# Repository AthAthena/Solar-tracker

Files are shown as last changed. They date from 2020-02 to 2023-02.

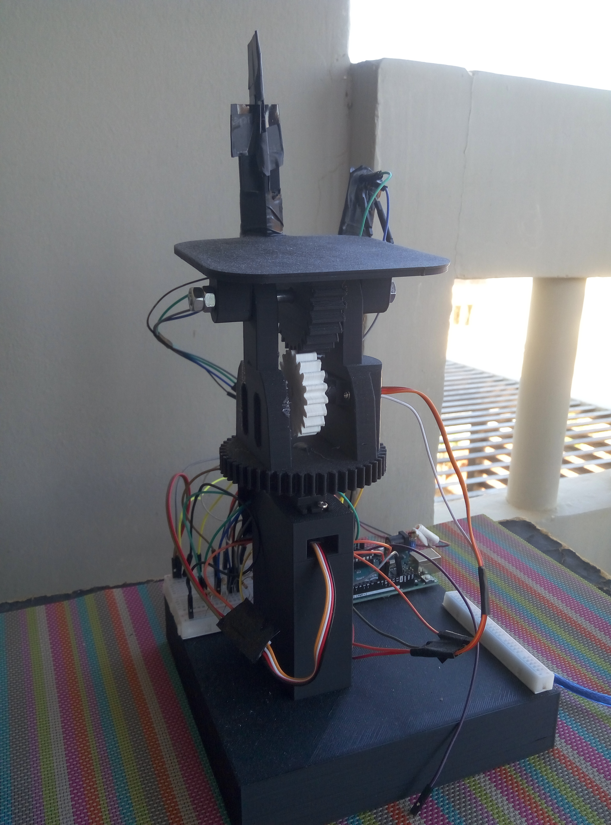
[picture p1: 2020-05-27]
P00513-165502[1].jpg

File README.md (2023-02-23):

ΕΠΑΛ ΚΙΣΑΜΟΥ-ΓΕΛ ΚΙΣΑΜΟΥ

ΛΙΓΑ ΛΟΓΙΑ ΓΙΑ ΤΗΝ ΠΕΡΙΠΕΤΕΙΑ ΤΗΣ ΚΑΤΑΣΚΕΥΗΣ ΜΑΣ
Η αναζήτηση άρχισε με σκοπό τη κατασκευή ενός solar tracker όπως του συναδέλφου https://www.thingiverse.com/thing:53321
ή https://www.instructables.com/id/Arduino-Solar-Tracker/ .
ΟΜΩΣ όλες αυτές οι κατασκευές είναι για εσωτερικό χώρο και για λόγους επίδειξης και όχι για ένα πραγματικό solar tracker.
Και εδώ μπήκαμε στην μεγάλη περιπέτεια κατασκευής ενός πραγματικού solar tracker και ως φυσική συνέπεια (ο καθηγητής μας είναι φυσικός και του αρέσει η αστροφυσική) και solar path finder- επιστημονικό εργαλείο εύρεσης των γωνίων που διαγράφει ο ΗΛΙΟΣ στην περιοχή μας.
ΚΑΙ ΑΝΑΣΧΕΔΙΑΣΑΜΕ ΤΑ ΠΑΝΤΑ ΕΞ ΑΡΧΗΣ!!!

Η ηλιακή ενέργεια αποτελεί ανανεώσιμη πηγή ενέργειας με πρόσφορη μέθοδο χρησιμοποίησή της τα φωτοβολταϊκά πάνελ. Όμως ο ήλιος αποδίδει τα μέγιστα μόνο όταν «πέφτει» κάθετα στο πάνελ, έτσι ψάχνουμε τρόπο να ακολουθεί το πάνελ τις ακτίνες του ήλιου. Ένας τρόπος παρακολούθησης του είναι με φωτοευαίσθητες αντιστάσεις οι οποίες παρακολουθούνται από τον μικροελεγκτή arduino και με servo ο μικροελεγκτής προσαρμόζει το πάνελ ώστε οι ακτίνες να πέφτουν κάθετα.

Υλικά (τελικός απολογισμός) :

1.arduino uno (https://grobotronics.com/funduino-uno-rev3-arduino-uno-compatible.html) = € 11.90 

2.   4 ldr (https://grobotronics.com/photo-resistor-ldr-5mm.html)=4*0,20=€ 0,80

3.  2 servo (link:  https://grobotronics.com/servo-small-5kg.cm-metal-gears-with-analog-feedback-feetech-fs9225m.html
https://grobotronics.com/analog-feedback-micro-servo-plastic-gear.html
 )=€9.90+€12.20=€21,10
 
4.wires (https://grobotronics.com/jumper-wires-15cm-female-to-male-pack-of-10.html ΚΑΙ https://grobotronics.com/jumper-wires-15cm-male-to-male-pack-of-10.html)=2*€1.80=€ 3,30

5..breadboard (link: https://grobotronics.com/breadboard-400-tie-point-white-half-size.html ) =€3.20

6.Bluetooth Module for Arduino - HC05 (https://grobotronics.com/bluetooth-module-for-arduino-hc05.html) =€6.80

7. 4 αντιστάσεις 1kohm (https://grobotronics.com/carbon-1-4w-5-1kohm.html) = €0,04

8.servo arm(https://grobotronics.com/servo-arm-double-5cm-horn-spline-25t.html)=€1.90

9.Πλαστικά γρανάζια απο 3D εκτυπωτή του εκφέ χανίων (ΤΑ STL ΑΡΧΕΙΑ ΠΕΡΙΛΑΜΒΑΝΟΝΤΑΙ ΩΣ ST1,ST2,..)
ΕΝΔΕΙΚΤΙΚΟ ΣΥΝΟΛΟ=€49,00

ΣΕ ΕΞΩΤΕΡΙΚΟ ΧΩΡΟ ΠΟΥ ΤΟ ΔΟΚΙΜΑΣΑΜΕ ΔΙΑΠΙΣΤΩΣΑΜΕ ΟΤΙ ΘΑ ΧΡΕΙΑΣΤΕΙ ΚΑΙ ΕΝΑ ΓΥΑΛΙΝΟ ΣΚΕΠΑΣΜΑ

ΠΕΡΙΓΡΑΦΗ ΠΡΟΒΛΗΜΑΤΟΣ
Η εποχή μας απαιτεί μεγάλα ενεργειακά αποθέματα , έτσι ένα αποδοτικό φωτοβολταικό πάνελ που ακολουθεί τον ήλιο μας δείχνει τον δρόμο στους κατασκευαστές φωτοβ.συστημάτων.Πόσο μάλλον όταν το πρότζεκτ μας καταγράφει τις γωνίες που δημιουργεί ο ήλιος στο στερέωμα στο καστέλι κισάμου και έτσι δείχνει ανα ημέρα και ώρα την κατάλληλη γωνία που πρέπει να έχει το φ. πάνελ για μέγιστη απόδοση.

Το μοίρασμα της γνώσης προτεραιότητα μας!
Μια επιστημονική εργασία αυτού του είδους εκπαιδεύει τους μελλοντικούς μας επιστήμονες στο διαθεματικό πλαίσιο STEM-ΘΕΤΙΚΕΣ ΕΠΙΣΤΗΜΕΣ-ΡΟΜΠΟΤΙΚΗ.
ΑΚΟΛΟΥΘΩΝΤΑΣ ΤΟ ΜΟΝΟΠΑΤΙ ΤΟΥ ΗΛΙΟΥ
Σε συνέχεια της προηγούμενης απάντησης η ιδέα μας είναι να κατασκευάσουμε ένα ηλιακό ανιχνευτή της πορείας του ήλιου που θα προσαρμόζει το φωτοβολταικό πάνελ μας κάθετα στις ακτίνες του ήλιου για να έχει την μέγιστη απόδοση και ταυτόχρονα θα καταγράφει τις γωνίες αυτές.Θα χρησιμοποιήσουμε 4 ldr φωτοαντιστάσεις-οι αισθητήρες φωτός που ανάλογα με το φως που λαμβάνουν θα δίνουν εντολή να στραφεί το πάνελ μας στη σωστή θέση- 2 σερβομηχανισμούς για να εκτελούν τις παραπάνω εντολές και θα αποτελούν συνάμα αισθητήρες κλίσης για την καταγραφή αυτών των γωνιών. Φυσικά και arduino που είναι ο εγκέφαλος της κατασκευής μας.
3D εκτυπωμένα εξαρτήματα θα δώσουν σταθερότητα και αποδοτικότητα στην κατασκευή μας.
Η ομάδα μας αποτελείται απο 3 μαθητές του ΓΕΛ Κισάμου β λυκείου με θαυμαστή όρεξη για μάθηση.
ΑΘΗΝΑ ΑΘΑΝΑΣΑΚΗ 
ΣΤΕΛΛΑ ΑΜΠΟΥΧΑΝΗ
ΣΠΥΡΟΣ ΕΙΡΗΝΑΚΗΣ
Τα κορίτσια είναι οι προγραμματίστριες του arduino και ο Σπύρος το πρακτικό μυαλό.
(Βέβαια οι απαιτήσεις του έργου ήταν να αναμιχθούν όλοι σε όλα τα στάδια της κατασκευής)
Ο Σπύρος βοήθησε και στο 3D σχεδιασμό εξαρτημάτων.
ΒΙΒΛΙΟΓΡΑΦΙΚΕΣ ΑΝΑΦΟΡΕΣ
1) https://en.wikipedia.org/wiki/Sun_path
2)https://en.wikipedia.org/wiki/Position_of_the_Sun
3)https://www.youtube.com/watch?v=lJVEubm9Ja8
4)https://www.instructables.com/id/Arduino-Solar-Tracker/

LINK ΠΟΥ ΒΟΗΘΗΣΕ ΣΤΗΝ ΒΑΘΜΟΝΟΜΗΣΗ-CALIBRATION SERVO : https://dronebotworkshop.com/analog-feedback-servo-motor/

ΓΙΑ ΤΟΝ ΔΙΑΓΩΝΙΣΜΟ ΤΗΣ ΕΛΛΑΚ ΠΑΡΑΠΕΜΠΩ ΣΤΟ GITHUB ΤΗΣ ΜΑΘΗΤΡΙΑΣ ΑΘΗΝΑΣ ΑΘΑΝΑΣΑΚΗ ΑΠΟ ΤΟΝ ΟΠΟΙΟ ΑΝΤΕΓΡΑΨΑ ΤΑ ΑΡΧΕΙΑ: https://github.com/Ampirath/Solar-Tracker
VIDEO LINK:  https://www.youtube.com/watch?v=TfUpVVRkGPY
ΜΑΘΗΤΕΣ : ΑΘΗΝΑ ΑΘΑΝΑΣΑΚΗ,ΣΤΕΛΛΑ ΑΜΠΟΥΧΑΝΗ ΚΑΙ ΣΠΥΡΟΣ ΕΙΡΗΝΑΚΗΣ-ΓΕΛ ΚΙΣΑΜΟΥ,ΕΠΑΛ ΚΙΣΑΜΟΥ

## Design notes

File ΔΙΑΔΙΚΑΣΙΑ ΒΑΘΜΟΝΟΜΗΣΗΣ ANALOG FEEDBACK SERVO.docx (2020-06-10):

ΔΙΑΔΙΚΑΣΙΑ ΒΑΘΜΟΝΟΜΗΣΗΣ ANALOG FEEDBACK SERVO

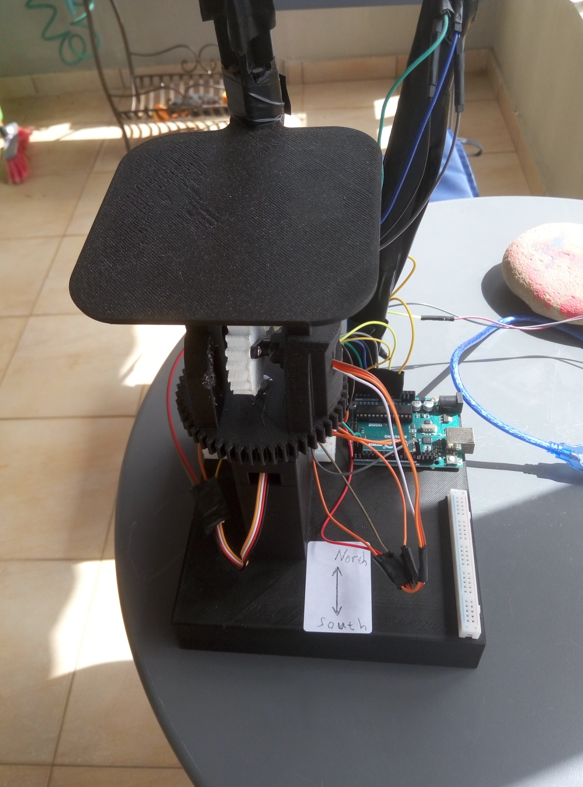
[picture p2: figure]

Κατά την τοποθέτηση προσέχουμε το κάτω servo να χει περιθώριο κινήσεων σε σχέση με τον νότο-south(βλέπε εικόνα) δεξιά –ανατολή 90⁰ ,αριστερά- δύση 90⁰ και με το πρόγραμμα recalibrationhorizontalservo.ino έχοντας σημαδέψει τις 90⁰ δεξιά αριστερά , βάζοντας σε //comment τις 35 και 36 γραμμές βρίσκουμε την αληθή αντιστοίχηση μεταξύ feedbackValue και γωνίας. Έπειτα προσθέτουμε τις γραμμές *

## feedbackValue = analogRead(feedbackPin);

## angle=map(feedbackValueh,84,424,-90,90);

## Βάζοντας στην θέση 84,424 τις τιμές που θα βρείτε εσείς και αντιστοιχούν στις γωνίες -90 ,90.

## *Τις γραμμές αυτές του κώδικα τις τοποθετείτε στην ίδια θέση του mainprogram.

## Αντίστοιχα εργαζόμαστε για το πάνω –vertical servo .Το πρόγραμμα CALIBRATIONANALOGSERVOvertical.ino ουσιαστικά είναι ίδιο με το recalibrationhorizontalservo.ino.

## Στο παρακάτω link αντλήσαμε πληροφορίες για την βαθμονόμηση αλλά και για αυτά τα analogfeedback servo:

## https://dronebotworkshop.com/analog-feedback-servo-motor/

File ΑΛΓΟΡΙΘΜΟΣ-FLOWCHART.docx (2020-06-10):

ΕΑΝ ΠΑΝΩ>ΚΑΤΩ

VERT.SERVO ΠΑΝΩ-ΒΟΡΕΙΑ

ΑΛΛΙΩΣ ΕΑΝ ΚΑΤΩ >ΠΑΝΩ

VERT.SERVO ΚΑΤΩ-ΝΟΤΙΑ

VERT,SERVO ΚΑΤΩ

ΕΑΝ ΟΙ ΔΕΞΙΟΙ-ΑΡΙΣΤΕΡΟΙ ΑΙΣΘΗΤΗΡΕΣ ΕΧΟΥΝ ΜΕΓΑΛΥΤΕΡΗ ΔΙΑΦΟΡΑ ΑΠΟ ΤΗΝ ΕΠΙΤΡΕΠΟΜΕΝΗ

↓

ΚΑΤΕΓΡΑΨΕ ΓΩΝΙΕΣ

1) γωνία ύψους-altitude και

2) azimuth-ΑΖΙΜΟΥΘΙΟ

VOID SETUP (ΤΡΕΧΕΙ ΜΙΑ ΦΟΡΑ)

ΑΡΧΙΚΟΠΟΙΗΣΗ ΣΕΙΡΙΑΚΗΣ ΕΠΙΚΟΙΝΩΝΙΑΣ

horizontal SERVO.attach PIN

vertical SERVO.attach PIN

ΧΡΗΣΙΜΟΠΟΙΗΣΗ SERVO ΒΙΒΛΙΟΘΗΚΗΣ

ΚΑΘΟΡΙΣΜΟΣ PIN ΓΙΑ ΚΑΤΩ-HORIZONTAL SERVO ΚΑΙ FEEDBACK ANALOG PIN ΚΑΙ ΟΡΙΑ-LIMITS SERVO

ΚΑΘΟΡΙΣΜΟΣ PIN ΓΙΑ ΠΑΝΩ-VERTICAL SERVO ΚΑΙ FEEDBACK ANALOG PIN ΚΑΙ ΟΡΙΑ-LIMOTS SERVO

ΚΑΘΟΡΙΣΜΟΣ ANALOG PIN ΓΙΑ LDR SENSOR

ΔΙΑΒΑΣΜΑ ΑΠΟ LDR SENSORS ΚΑΙ ΥΠΟΛΟΓΙΣΜΟΣ ΜΕΣΩΝ ΤΙΜΩΝ LDR ,ΠΑΝΩ-ΚΑΤΩ ΚΑΙ ΔΕΞΙΑ ΑΡΙΣΤΕΡΑ

ΕΑΝ ΟΙ ΠΑΝΩ- ΚΑΤΩ ΑΙΣΘΗΤΗΡΕΣ ΕΧΟΥΝ ΜΕΓΑΛΥΤΕΡΗ ΔΙΑΦΟΡΑ ΑΠΟ ΤΗΝ ΕΠΙΤΡΕΠΟΜΕΝΗ

↓

ΚΑΤΕΓΡΑΨΕ ΓΩΝΙΕΣ

1) γωνία ύψους-altitude και

2) azimuth-ΑΖΙΜΟΥΘΙΟ

ΕΑΝ ΔΕΞΙΟΙ>ΑΡΙΣΤΕΡΟΙ

HORIZ.SERVO ΔΕΞΙΑ-ΑΝΑΤΟΛΙΚΑ

ΑΛΛΙΩΣ ΕΑΝ ΑΡΙΣΤΕΡΟΙ>ΔΕΞΙΟΙ

HORIZ.SERVO ΑΡΙΣΤΕΡΑ-ΔΥΤΙΚΑ

VOID LOOP (ΕΠΑΝΑΛΑΜΒΑΝΟΜΕΜΗ ΛΟΥΠΑ)

MAP-ΧΑΡΤΗΣ ΠΟΥ ΠΡΟΕΚΥΨΕ ΜΕΤΑ ΑΠΟ CALIBRATION Α)ΓΙΑ ΑΖΙΜΟΥΘΙΟ-AZIMUTH

,, Β)ΓΙΑ ΥΨΟΣ-ALTITUDE

ΑΡΧΗ ΠΡΟΓΡΑΜΜΑΤΟΣ

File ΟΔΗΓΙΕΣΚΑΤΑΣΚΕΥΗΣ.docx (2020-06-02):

Υλικά (τελικός απολογισμός) :

1.arduino uno (https://grobotronics.com/funduino-uno-rev3-arduino-uno-compatible.html) = € 11.90
2. 4 ldr (https://grobotronics.com/photo-resistor-ldr-5mm.html)=4*0,20=€ 0,80
3. 2 servo (link: https://grobotronics.com/servo-small-5kg.cm-metal-gears-with-analog-feedback-feetech-fs9225m.html
https://grobotronics.com/analog-feedback-micro-servo-plastic-gear.html
)=€9.90+€12.20=€21,10
4.wires (https://grobotronics.com/jumper-wires-15cm-female-to-male-pack-of-10.html ΚΑΙ https://grobotronics.com/jumper-wires-15cm-male-to-male-pack-of-10.html)=2*€1.80=€ 3,30
5..breadboard (link: https://grobotronics.com/breadboard-400-tie-point-white-half-size.html ) =€3.20
6.Bluetooth Module for Arduino – HC05 (https://grobotronics.com/bluetooth-module-for-arduino-hc05.html) =€6.80

7. 4 αντιστάσεις 1kohm (https://grobotronics.com/carbon-1-4w-5-1kohm.html) = €0,04

8.servo arm(https://grobotronics.com/servo-arm-double-5cm-horn-spline-25t.html)=€1.90
9.Πλαστικά γρανάζια απο 3D εκτυπωτή του εκφέ χανίων (ΤΑ STL ΑΡΧΕΙΑ ΠΕΡΙΛΑΜΒΑΝΟΝΤΑΙ ΩΣ ST1,ST2,..)
ΕΝΔΕΙΚΤΙΚΟ ΣΥΝΟΛΟ=€49,00

Η ιδέα μας είναι να κατασκευάσουμε ένα ηλιακό ανιχνευτή της πορείας του ήλιου που θα προσαρμόζει το φωτοβολταικό πάνελ μας κάθετα στις ακτίνες του ήλιου για να έχει την μέγιστη απόδοση και ταυτόχρονα θα καταγράφει τις γωνίες αυτές. Θα χρησιμοποιήσουμε 4 ldr φωτοαντιστάσεις-οι αισθητήρες φωτός που ανάλογα με το φως που λαμβάνουν θα δίνουν εντολή να στραφεί το πάνελ μας στη σωστή θέση- 2 σερβομηχανισμούς για να εκτελούν τις παραπάνω εντολές και θα αποτελούν συνάμα αισθητήρες κλίσης για την καταγραφή αυτών των γωνιών. Φυσικά και arduino που είναι ο εγκέφαλος της κατασκευής μας. 3D εκτυπωμένα εξαρτήματα θα δώσουν σταθερότητα και αποδοτικότητα στην κατασκευή μας.

ΚΑΤΑΣΚΕΥΗ

Τα σχεδιασμένα 3d εξαρτήματα απο την ομάδα μας θα τα βρείτε ως stl αρχεία στο github.Τα servo που είναι στη λίστα μας «κουμπώνουν» ακριβώς στα παραπάνω εξαρτήματα.

Το servo : https://grobotronics.com/servo-small-5kg.cm-metal-gears-with-analog-feedback-feetech-fs9225m.html

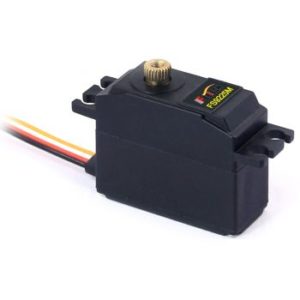
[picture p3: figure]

«κουμπώνει» στο 3d εξάρτημα base.stl (ή stl 1).

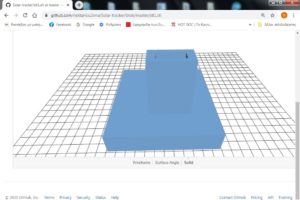
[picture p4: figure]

Πάνω στο servo βάζουμε το servo arm (https://grobotronics.com/servo-arm-double-5cm-horn-spline-25t.html) .

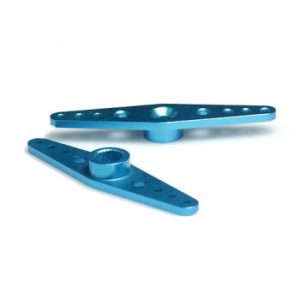
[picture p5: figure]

ΟΠΩΣ ΣΤΗΝ ΕΙΚΟΝΑ 1

ΕΙΚΟΝΑ1:

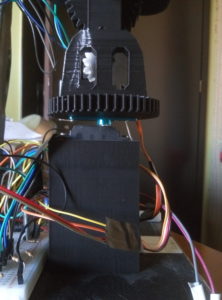
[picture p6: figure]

Πάνω στο servoarm βιδώνουμε το 3d εξάρτημα panel-mount.stl (ή stl2)

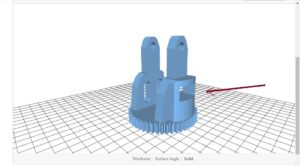
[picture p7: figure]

και τοποθετούμε το 2ο servo (εκεί που δείχνει το βέλος)

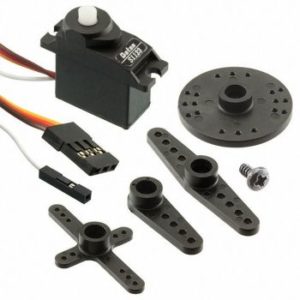
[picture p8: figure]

στο κατάλληλο άνοιγμα του panel-mount.stl, όπως την εικόνα 2:

ΕΙΚΟΝΑ2

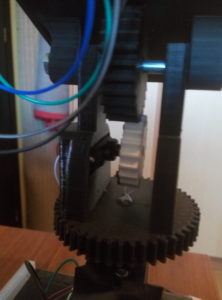
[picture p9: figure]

Στο 2ο servo βιδώνουμε το Vertical_Servo_Gear.stl (ή stl5, το άσπρο στην εικόνα2 )

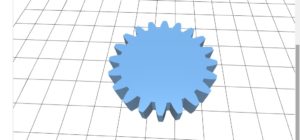
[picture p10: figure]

όπως στην εικόνα 2.

Στο Panel_Bracket2.stl(ή stl4)

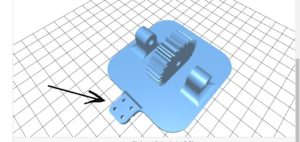
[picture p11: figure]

τοποθετούμε το LDR DIVIDER HIGH.stl(ή stl3) εκεί που δείχνει το βέλος (έχει υποδοχή να το δεχτεί και ας μην φαίνεται στην πανω εικόνα).

LDR DIVIDER HIGH.stl:

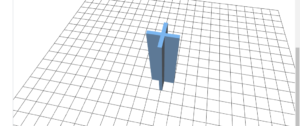
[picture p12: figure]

Τέλος με την κατάλληλη βίδα 4mm με μήκος 9cm και τα αντίστοιχα παξιμάδια τοποθετούμε το Panel_Bracket2.stl όπως στην εικόνα 2.

Η συνδεσμολογία πρέπει να γίνει όπως

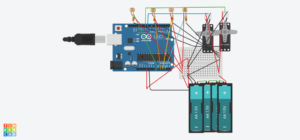
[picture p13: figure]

ΟΛΑ TA ΑΡΧΕΙΑ ΒΡΙΣΚΟΝΤΑΙ ΣΤΟ GITHUB ΜΕ ΜΕΓΑΛΥΤΕΡΗ ΑΝΑΛΥΣΗ.

Έπειτα έπρεπε να βαθμονομήσουμε τα servo ώστε να μετράνε την σωστή γωνία και σε αυτήν την επίπονη διαδικασία βοήθησε το 2ο link.

Ο διαιρέτης τάσης που φαίνεται στο κύκλωμα που βρίσκεται στο github λειτούργησε καλά τελικά σε εξωτερικό χώρο με αντιστάσεις 1 kohm(4 αντιστάσεις).

ΒΙΒΛΙΟΓΡΑΦΙΚΕΣ ΑΝΑΦΟΡΕΣ

1. https://en.wikipedia.org/wiki/Sun_path 2)https://en.wikipedia.org/wiki/Position_of_the_Sun 3)https://www.youtube.com/watch?v=lJVEubm9Ja8 4)https://www.instructables.com/id/Arduino-Solar-Tracker/
2. LINK ΠΟΥ ΒΟΗΘΗΣΕ ΣΤΗΝ ΒΑΘΜΟΝΟΜΗΣΗ-CALIBRATION SERVO : https://dronebotworkshop.com/analog-feedback-servo-motor/

ΣΤΟ LINK ΠΟΥ ΑΚΟΛΟΥΘΕΙ ΚΑΙ ΑΝΗΚΕΙ ΟΠΩΣ ΚΑΙ ΔΗΜΙΟΥΡΓΗΘΗΚΕ ΑΠΟ ΤΗΝ ΟΜΑΔΑ ΤΩΝ ΜΑΘΗΤΩΝ ΠΟΥ ΕΡΓΑΣΤΗΚΕ ΓΙ ΑΥΤΟ ΤΟ PROJECT ΕΙΝΑΙ ΤΟΠΟΘΕΤΗΜΕΝΑ ΟΛΑ ΤΑ ΑΡΧΕΙΑ ΠΟΥ ΕΙΝΑΙ ΑΝΑΓΚΑΙΑ ΓΙΑ ΤΗΝ ΚΑΤΑΝΟΗΣΗ ΚΑΙ ΚΑΤΑΣΚΕΥΗ ΑΝΑΛΟΓΟΥ ΕΓΧΕΙΡΗΜΑΤΟΣ LINK: https://github.com/Ampirath/Solar-Tracker

LINK VIDEO ΠΟΥ ΦΤΙΑΧΤΗΚΕ ΑΠΟ ΤΑ ΠΑΙΔΙΑ: https://www.youtube.com/watch?v=TfUpVVRkGPY

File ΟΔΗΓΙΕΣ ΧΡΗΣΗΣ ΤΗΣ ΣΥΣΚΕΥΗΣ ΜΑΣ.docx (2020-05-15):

ΟΔΗΓΙΕΣ ΧΡΗΣΗΣ ΤΗΣ ΣΥΣΚΕΥΗΣ ΜΑΣ-Η ΕΚΔΟΧΗ ΜΕ ΤΑ ANALOG FEEDBACK SERVO

Εφόσον έχουμε εκτυπώσει τα 3D εξαρτήματά μας και έχουμε πραγματοποιήσει την συνδεσμολογία που φαίνεται στο png αρχείο (και στο brd από το tinkercad) φορτώνουμε στο arduino το προγραμμά μας (MAINPROGRAM.ino).

Επειτα έχοντας κατεβάσει στο κινητό μας από το google play ή από όπου θέλουμε μια εφαρμογή που μας δείχνει τον πραγματικό βορά ( gps true north) τοποθετούμε την συσκευή όπως την εικόνα που είναι στην επόμενη σελίδα (παρατηρήστε το άσπρο αυτοκόλλητο που δείχνει την σωστή τοποθέτηση).


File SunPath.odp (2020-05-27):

## Βρίσκοντας το μονοπάτι του ήλιου

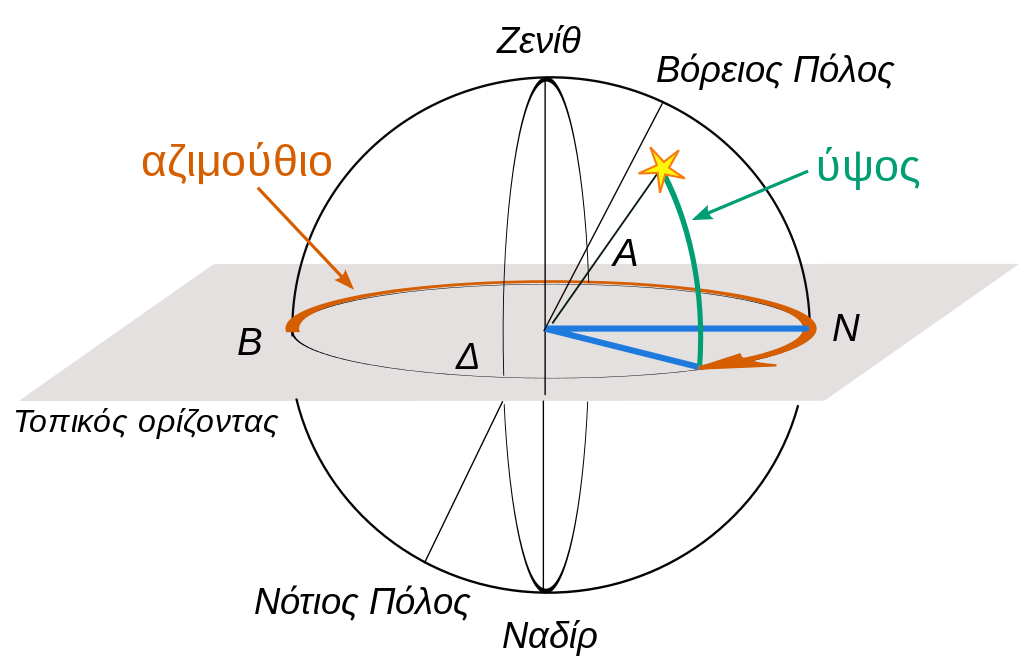
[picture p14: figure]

## Η διαδρομή του ήλιου

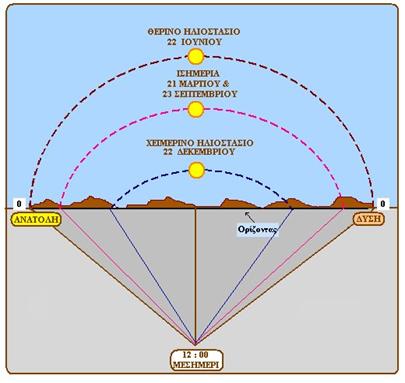
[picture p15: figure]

## Ύψος ήλιου (κλίση επιφάνειας) (altitude)

  Το ύψος του ήλιου αναφέρεται στη γωνία που σχηματίζει ο ήλιος με τον ορίζοντα της Γης. Αφού ειναι γωνία, μετριέται σε μήρες.
  Η κλίση είναι 0° στην ανατολή του ηλίου και στην δύση του και μπορεί να φτάσει τις 90° (ζενίθ) το μεσημέρι, σε μέρη κοντά στον ισημερινό.
  Λόγω της κλίσης του άξονα περιστροφής της γης η θέση του ήλιου στον ουρανό του ισημερινού το μεσημέρι θα αποκλίνει στη διάρκεια του έτους κατά +/- 23.5 μοίρες από το απολύτως κάθετο (ζενίθ).

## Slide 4

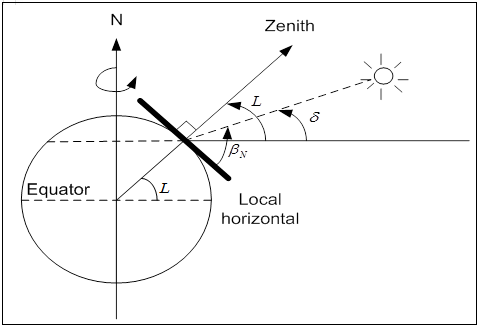
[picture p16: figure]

## Γωνία αζιμούθιου (azimuth)

  Είναι η γωνία προς την οποία ειναι στραμμένη μια επιφάνεια.
  Συνήθως μετριέται απο το Βορρά (0° / 360°) προς την Ανατολή.

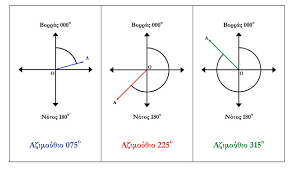
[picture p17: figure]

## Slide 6

  Ή μπορούμε ανάλογα το ημισφαίριο να το ορίσουμε διαφορετικά.
  Για τοποθεσίες του βόρειου ηµισφαιρίου µηδενική τιµή του αζιμούθιου γ αντιστοιχεί σε νότια κατεύθυνση, θετικές τιµές του αναφέρονται σε δυτικούς προσανατολισµούς, και αρνητικές τιµές του γ σε ανατολικούς προσανατολισµούς.

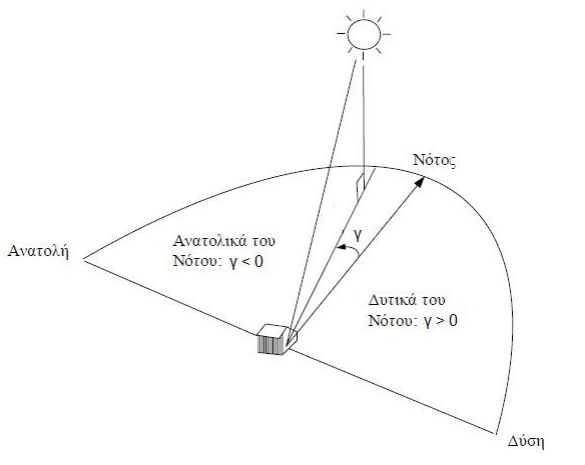
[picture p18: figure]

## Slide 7

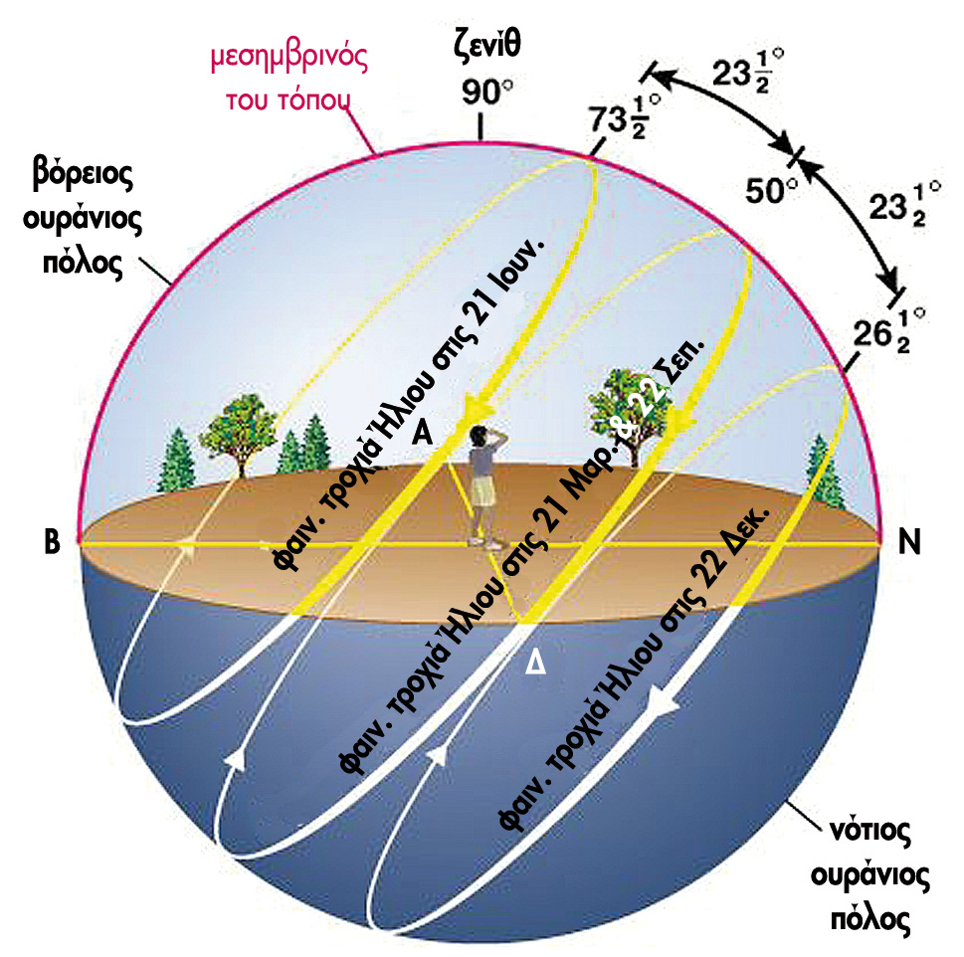
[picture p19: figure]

  Αθηνά Μαρία Αθανασάκη – ΓΕΛ Κισάμου

## ΠΗΓΕΣ

- Motions of the Sun simulator (https://ccnmtl.github.io/astro-simulations/sun-motion-simulator/)
- Sun Path (wikipedia) (https://en.wikipedia.org/wiki/Sun_path)
- Position of the Sun (wikipedia) (https://en.wikipedia.org/wiki/Position_of_the_Sun)
- Solar altitude (https://sciencing.com/solar-altitude-23364.html)
- Solar Zenith Angle (wikipedia) (https://en.wikipedia.org/wiki/Solar_zenith_angle)
- Solar Azimuth (wikipedia) (https://en.wikipedia.org/wiki/Solar_azimuth_angle)
- Διάγραμμα μονοπατιού (https://www.sunearthtools.com/dp/tools/pos_sun.php)
- Μονοπάτι του Ήλιου στην Αθήνα (https://acomelectronics.com/forum/viewtopic.php?t=20)
- Ηλιακή Ακτινοβολία - Γεωμετρία

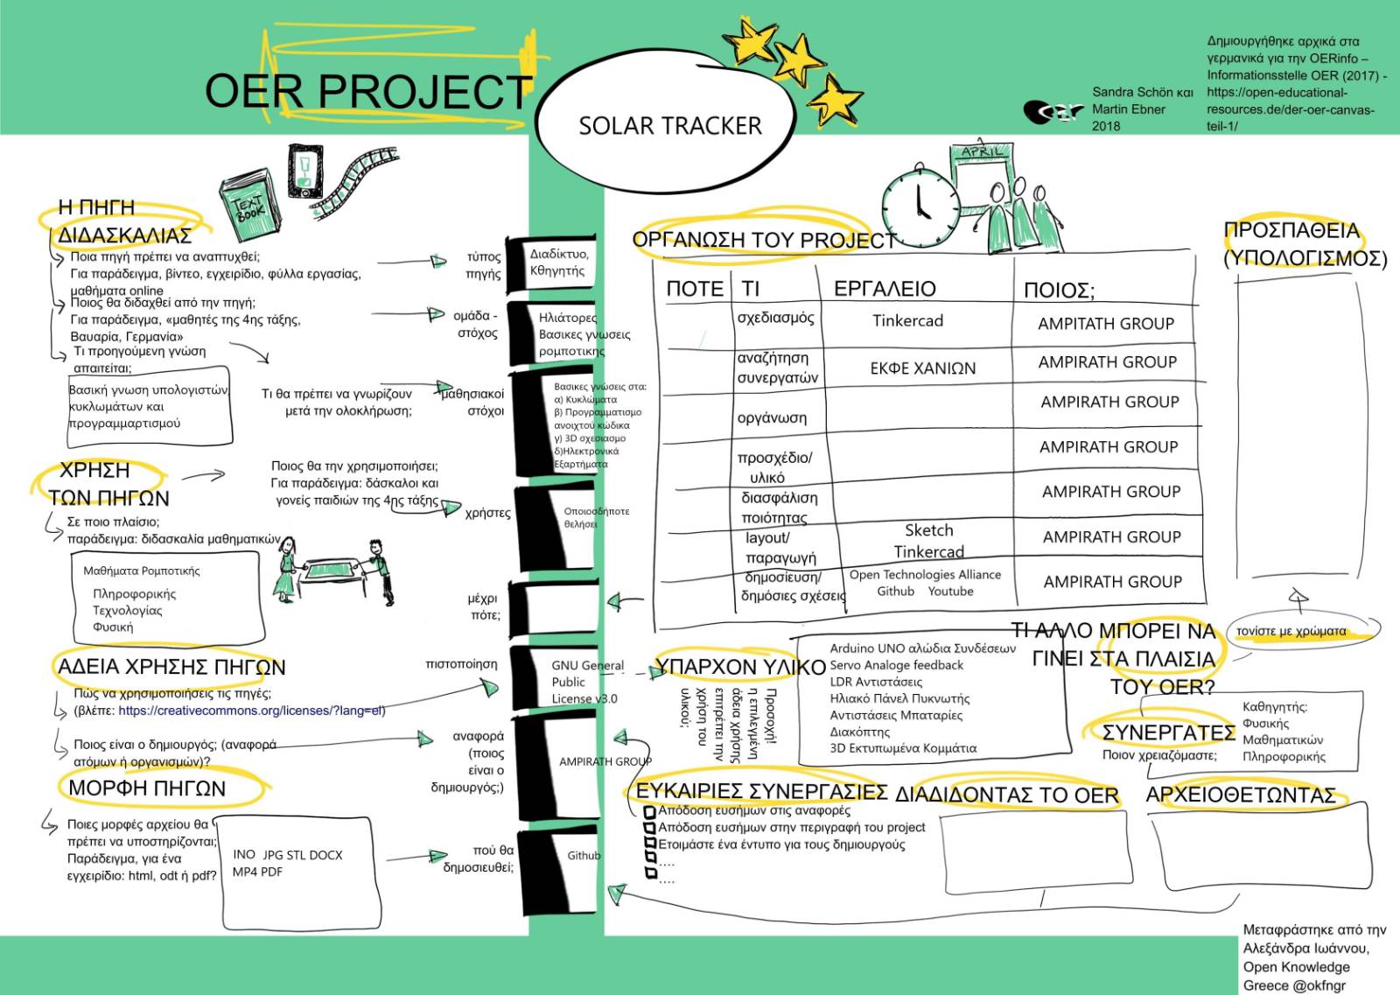
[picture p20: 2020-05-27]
OERCANVAS.jpg

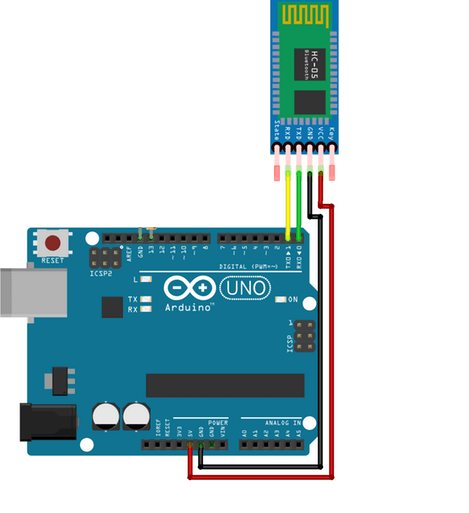
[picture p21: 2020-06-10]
hc-05-connection-Circuit.png

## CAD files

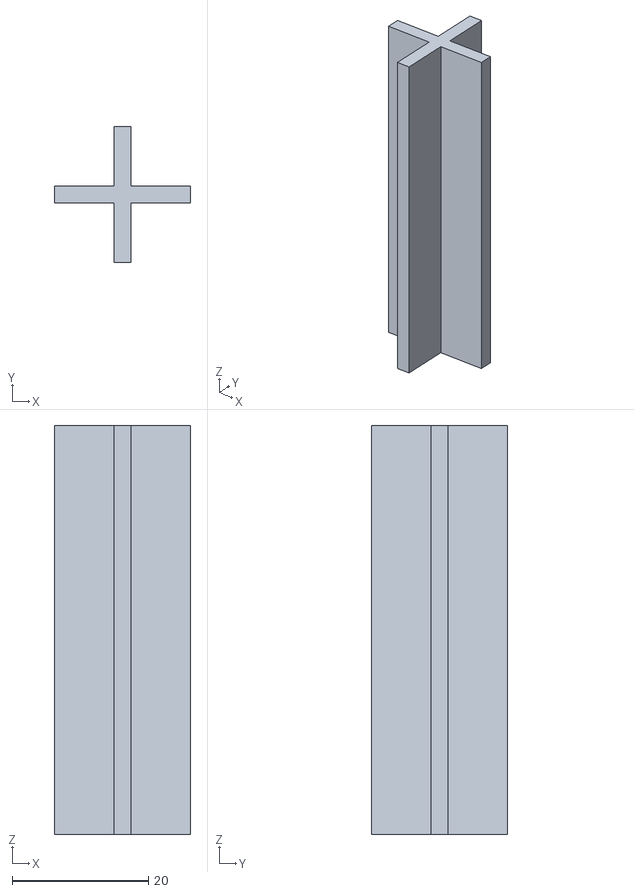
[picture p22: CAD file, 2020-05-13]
stl3.stl
20.0 x 20.0 x 60.0

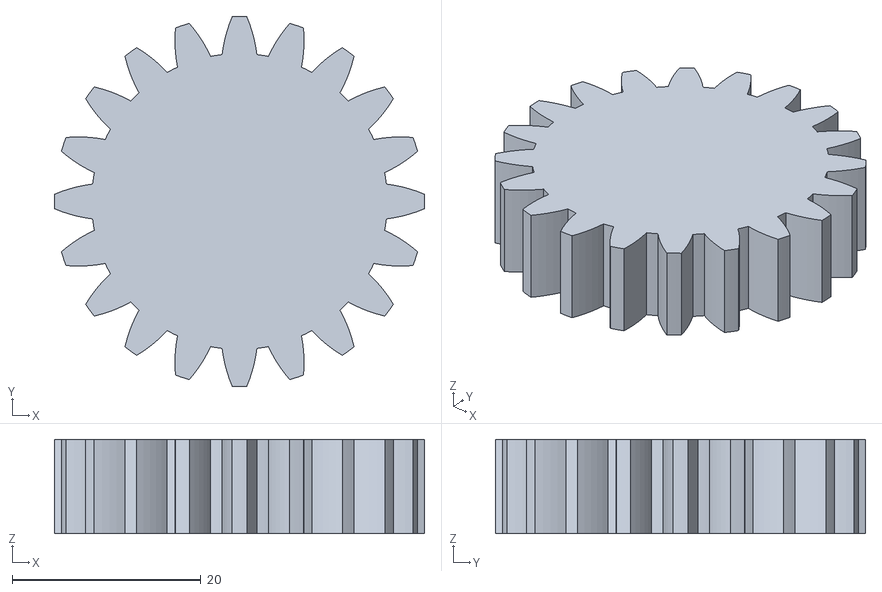
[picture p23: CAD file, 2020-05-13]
stl5.stl
39.2 x 39.2 x 10.0

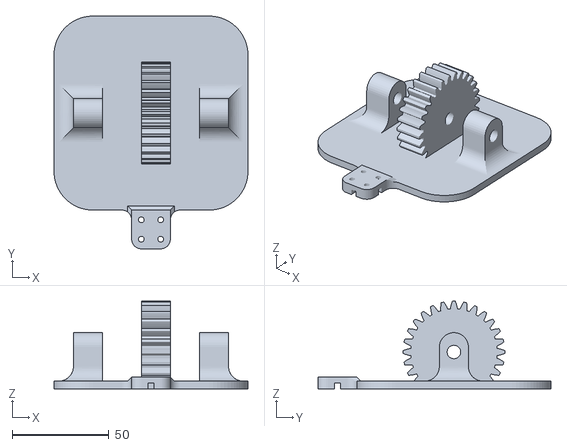
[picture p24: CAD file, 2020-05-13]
stl4.stl
100.0 x 120.0 x 45.2

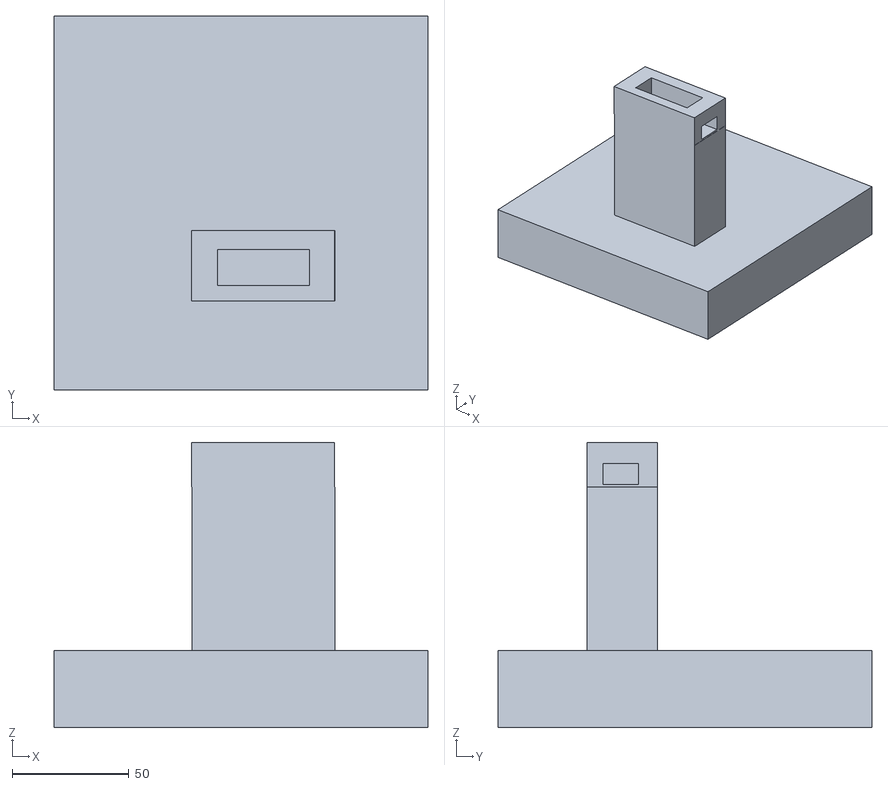
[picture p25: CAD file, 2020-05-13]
stl1.stl
160.0 x 160.0 x 122.1

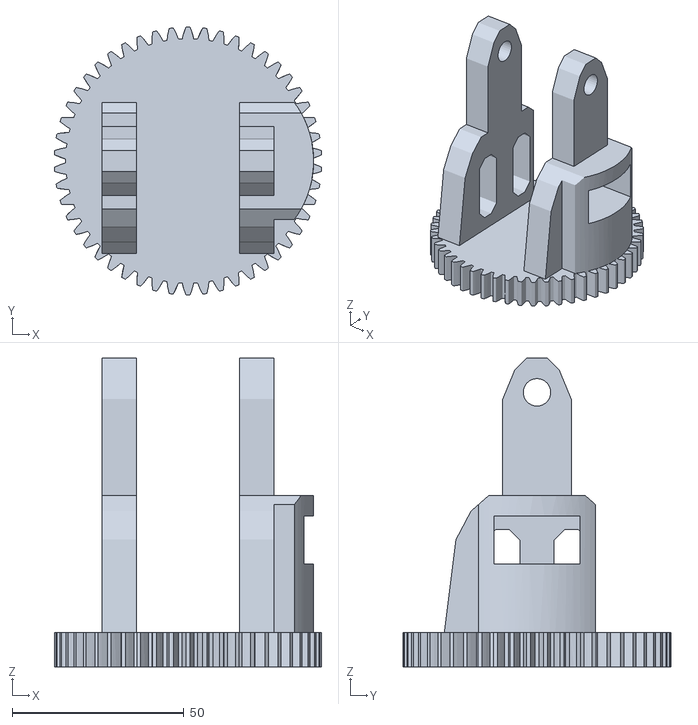
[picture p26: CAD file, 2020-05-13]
stl2.stl
77.9 x 78.0 x 90.0

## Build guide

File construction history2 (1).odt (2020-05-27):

Solar Path Finder

Ιστορικό κατασκεύης

Ξεκινήσαμε κάνοντας εβδομαδιαία μαθήματα ρομποτικής με τον Κ. Κουράκη. Άφου μάθαμε τα βασικά γύρω απο τα κυκλώματα, τον προγραμματισμό και το arduino, προχωρήσαμε σε διάφορες μικρές εργασίες-project για να γίνουμε πιο οικείοι με το arduino.

Μετά από ψάξιμο στο ίντερνετ καταλήξαμε ότι η κατασκευή με την οποία θέλαμε να ασχοληθούμε ήταν ένα solar finder, μιάς και είναι μια συσκευή μέσα στην επικαιρότητα των ημερών αλλά και προσφέρει πολλά περιθώρια για εξέλιξη και πειραματισμό.

Από τις παρακάτω πηγές, πήραμε την αρχική ιδέα για το πως θα έπρεπε να μοιάζει η συσκευή, τη λογική της λειτουργίας της και τον τρόπο προγραμματισμού της.

https://www.instructables.com/id/Arduino-Solar-Tracker/

και τα 3d stl αρχεία από:

https://www.thingiverse.com/thing:53321

(Τα οποία τελικά τα ανασχεδιάσαμε με το online tinkercad)

Έτσι με βάση αυτές, φτιάξαμε μια πρόχειρη κατασκευή χρησιμοποιώντας υλικά απο παιδικά παιχνίδια για να διαπιστώσουμε αν το solar tracker, όντως δούλευε όπως έπρεπε.

Αφού η δοκιμή ολοκληρώθηκε με μερική αποτυχία ,αναγκαστήκαμε να κατανοήσουμε πληρώς το hardware-software και με πολλές διορθώσεις και αλλαγές η 5η δοκιμή μας κατέληξε σε επιτυχία. Ζητήσαμε απο το ΕΚΦΕ Χανίων να μας εκτυπώσει τα 3D κομμάτια που χρειαζόμασταν.

Ξεκινήσαμε γράφοντας ένα απλό πρόγραμμα, ώστε το φωτοβολταϊκό να στρέφεται προς την κατεύθυνση με το περισσότερο φως. Αποφασίσαμε όμως ότι μια ακόμα χρήσιμη εφαρμογή του solar path finder θα ήταν η αποστολή δεδομένων της θέσης του. Με αυτό τον τρόπο μπορούμε να έχουμε καταγραφή των γωνιών που διαγράφει και έτσι, όταν τοποθετείται σε εξωτερικό χώρο, παίρνουμε ξεκάθαρη εικόνα του μονοπατιού του ήλιου σε εκείνη την περιοχή.

Για να το κάνουμε αυτό έπρεπε πρώτα να κατανοήσουμε τον τρόπο με τον οποίο κινείται ο ήλιος και το πως γίνονται αυτές οι μετρήσεις στην πραγματικότητα, ώστε να βρούμε ενα τρόπο για να το κάνουμε μέσω της κατασκευής μας.

Αρχικά προσπαθήσαμε να το κάνουμε με την βοήθεια ενός αισθητήρα επιτάχυνσης-γυροσκοπίου-μαγνητόμετρου, όμως αποδείχθηκε ότι δεν ήταν εύκολο και το ποσοστό σφάλματος ήταν μεγάλο. Με επίπονη βαθμονόμηση-calibration τελικά δούλεψε ικανοποιητικά αλλά ο καθηγητής ,μας προέτρεψε να ασχοληθούμε-εξελίξουμε έναν πιο απλό τρόπο εύρεσης των γωνιών του Ήλιου. Οπότε αποφασίσαμε να αντικαταστήσουμε τα δύο απλά servo με αυτά που στέλνουν πίσω τη θέση στην οποία βρίσκεται το servo σωστά. ( analogfeedback servo).

Μη θέλοντας να διαλύσουμε την πρώτη μας κατασκευή, αποφασίσαμε να ξαναφτιάξουμε ολόκληρο το solar path finder από το μηδέν, κάνοντας ταυτόχρονα και κάποιες διορθώσεις στην δομή του, για να γίνεται πιό σωστή και ομαλή η λειτουργεία του.

Τελικά επανασχεδιάσαμε τα 3d εξαρτήματα 1)για να μπουν τα καινούργια-διαφορετικών διαστάσεων servo στην θέση των παλιών

2)για να μπορεί η κατασκευή να δουλέψει σε εξωτερικό χώρο και να μετράει σωστά τις γωνίες altitude,azimuth του Ήλιου (η πηγή μας και ο αντίστοιχος δημιουργός της https://www.thingiverse.com/thing:53321 - προνόησε μόνο μια κατασκευή επίδειξης -απλά solar tracker- για εσωτερικό χώρο).

Για να σιγουρευτούμε ότι οι τιμές που παίρναμε απο το servo ήταν σωστές, κάναμε κάποιες δοκιμές , βαθμονόμηση των servo(calibration).

Καταλήξαμε στην δημιουργία χαρτών -map, ώστε να γίνει αναλογία των τιμών που έδινε με τις πραγματικές.

Έπειτα, ξαναγράψαμε το πρόγραμμα του solar path finder κάνοντας τις απαραίτητες αλλαγές και το δοκιμάσαμε αρκετές φορές, ώστε να λύσουμε τυχόν σφάλματα που παρουσίαζε στην λειτουργία του.

Με το δικό μας λογισμικό μπορεί να γινεί live αναπαραγωγή των δεδομένων που συλλέγει το solar path finder και έτσι οποιοσδήποτε και απο οπουδήποτε να έχει πρόσβαση σε αυτές τις πληροφοριές τις οποίες μπορεί να χρησιμοποιήσει για τις δικές του εργασίες.

ΓΕΛ – ΕΠΑΛ ΚΙΣΑΜΟΥ(ΣΥΝΕΡΓΑΣΙΑ)

Οι μαθητές :

ΑΘΗΝΑ ΑΘΑΝΑΣΑΚΗ

ΣΠΥΡΙΔΩΝ ΕΙΡΗΝΑΚΗΣ

ΣΤΕΛΛΑ ΑΜΠΟΥΧΑΝΗ

Ο επιβλέπων καθηγητής:

ΚΟΥΡΑΚΗΣ ΝΕΚΤΑΡΙΟΣ

ΣΥΝΤΑΚΤΗΣ:ΑΘΗΝΑ ΑΘΑΝΑΣΑΚΗ

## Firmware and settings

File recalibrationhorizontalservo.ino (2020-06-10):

// Include Arduino Servo Library
#include <Servo.h>
 
// Control and feedback pins
int servoPin = 9;
int feedbackPin = A0;
int angle; 
// Value from feedback signal
int feedbackValue;
 
// Create a servo object
Servo myservo;
 
void setup()
{
  // Setup Serial Monitor
  Serial.begin(9600);
  
  // Attach myservo object to control pin
  myservo.attach(servoPin);
  
  // Home the servo motor
  myservo.write(0);
  
  
 
    for (int servoPos = 0; servoPos <=180; servoPos = servoPos + 3){
    
    // Position servo motor
    myservo.write(servoPos);
    // Allow time to get there
    delay(2000);
    
    // Read value from feedback signal  
    feedbackValueh = analogRead(feedbackPinh);//comment this 2 lines 35 and 36 until you find the true matching between feedbackValue and angle 
    angle=map(feedbackValueh,84,424,-90,90);
    // Write value to serial monitor
    Serial.print("Position = ");
    Serial.print(angle);
    Serial.print("\t");
    Serial.println(feedbackValue);
  
  }
 
  // Move back to home position
  myservo.write(0);
  
  // Print to serial monitor when done
  Serial.println("Finished!");
 
}  
 
void loop()
{ 
myservo.write(0);
  
  
    for (int servoPos = 0; servoPos <=180; servoPos = servoPos + 3){
    
    // Position servo motor
    myservo.write(servoPos);
    // Allow time to get there
    delay(2000);
    
    // Read value from feedback signal
    feedbackValue = analogRead(feedbackPin);
    angle=map(feedbackValueh,84,424,-90,90);
 
    // Write value to serial monitor
    Serial.print("Position = ");
    Serial.print(angle);
    Serial.print("\t");
    Serial.println(feedbackValue);
  
  }
 
  // Move back to home position
  myservo.write(0);
  
  // Print to serial monitor when done
  Serial.println("Finished!");
  
}

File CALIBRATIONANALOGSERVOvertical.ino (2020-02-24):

/*
  Analog Feedback Servo Calibration Demo
  feedback_servo_calib.ino
  Uses S1213 Analog Feedback Servo Motor
  Results displayed on Serial Monitor
 
  DroneBot Workshop 2019
  https://dronebotworkshop.com
*/
 
// Include Arduino Servo Library
#include <Servo.h>
 
// Control and feedback pins
int servoPin = 9;
int feedbackPin = A0;
 
// Value from feedback signal
int feedbackValue;
int altitude; 
// Create a servo object
Servo myservo;
 
void setup()
{
  // Setup Serial Monitor
  Serial.begin(9600);
  
  // Attach myservo object to control pin
  myservo.attach(servoPin);
  
  // Home the servo motor
  myservo.write(0);
  
  // Step through servo positions
  // Increment by 5 degrees
  for (int servoPos = 0; servoPos <=155; servoPos = servoPos + 3){
    
    // Position servo motor
    myservo.write(servoPos);
    // Allow time to get there
    delay(2000);
    
    // Read value from feedback signal
    feedbackValue = analogRead(feedbackPin);
    altitude=map(feedbackValue,127,492,8,120);
    // Write value to serial monitor
    Serial.print("Position = ");
    Serial.print(servoPos);
    Serial.print("\t");
    Serial.print(" altitude = ");
    Serial.print(altitude);
    Serial.print("\t");
    Serial.println(feedbackValue);
  //micro analogservo 8moires ->127 , ,90MOIRES  392,120moires ->487
  }
 
  // Move back to home position
  myservo.write(0);
  
  // Print to serial monitor when done
  Serial.println("Finished!");
 
}  
 
void loop()
{ 
  delay(100);
   myservo.write(123);
  
}
